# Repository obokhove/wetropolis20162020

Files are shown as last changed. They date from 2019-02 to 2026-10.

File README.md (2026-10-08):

# Wetropolis Design 2016-present & Wetropolis spin-off projects (scroll down)

## Introduction
The Wetropolis flood demonstrator is a conceptual, physical installation showcasing what an extreme rainfall event is and how such an event can lead to extreme flooding of a city. A layman's introduction to Wetropolis is found in the following blog:
https://research.reading.ac.uk/dare/2017/07/25/wetropolis-flood-demonstrator/
Please read the blog first. Wetropolis is best experienced in person but, second best, please watch the following movies (from 30-08-2016):
- Exploring Wetropolis (movie for everyone October 2022): https://www.youtube.com/watch?v=rNgEqWdafKk
- News item October 11, 2022: https://mpecdt.ac.uk/exploring-wetropolis-an-extreme-rainfall-and-flood-demonstrator/
- a test to give a first impression https://youtu.be/1FIHFOn6IPQ
- the equivalent of the River Aire Boxing Day flood of 2015 with city flooding resulting from two wd's (one Wetropolis day wd=10s) of consecutive extreme 90% rainfall (so 18s of rainfall in 20s) https://youtu.be/N4Sp5gHXcz4
- EGU highligh article, peer-reviewed in international scientific journal (under education & communication): https://www.hydrol-earth-syst-sci.net/24/2483/2020/ (also read the interesting discussions under "Peer review")
- Impact Case Study Research Excellence Framework UK: "Flood mitigation: from outreach demonstrator to a graphical cost-effectiveness diagnostic for policy makers" 2021/2022. https://results2021.ref.ac.uk/impact/0ad7c1be-8e91-4aac-ab57-6c1e873cd3f1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" 
- Feedback from showcasings is found in the feedback folder: https://github.com/obokhove/wetropolis20162020/tree/master/feedback
- People travel around and showcase Wetropolis upon request and, these days, with adequate social distancing. Just contact us: onnobokhove@gmail.com (UK) & zweers@dds.nl (NL)

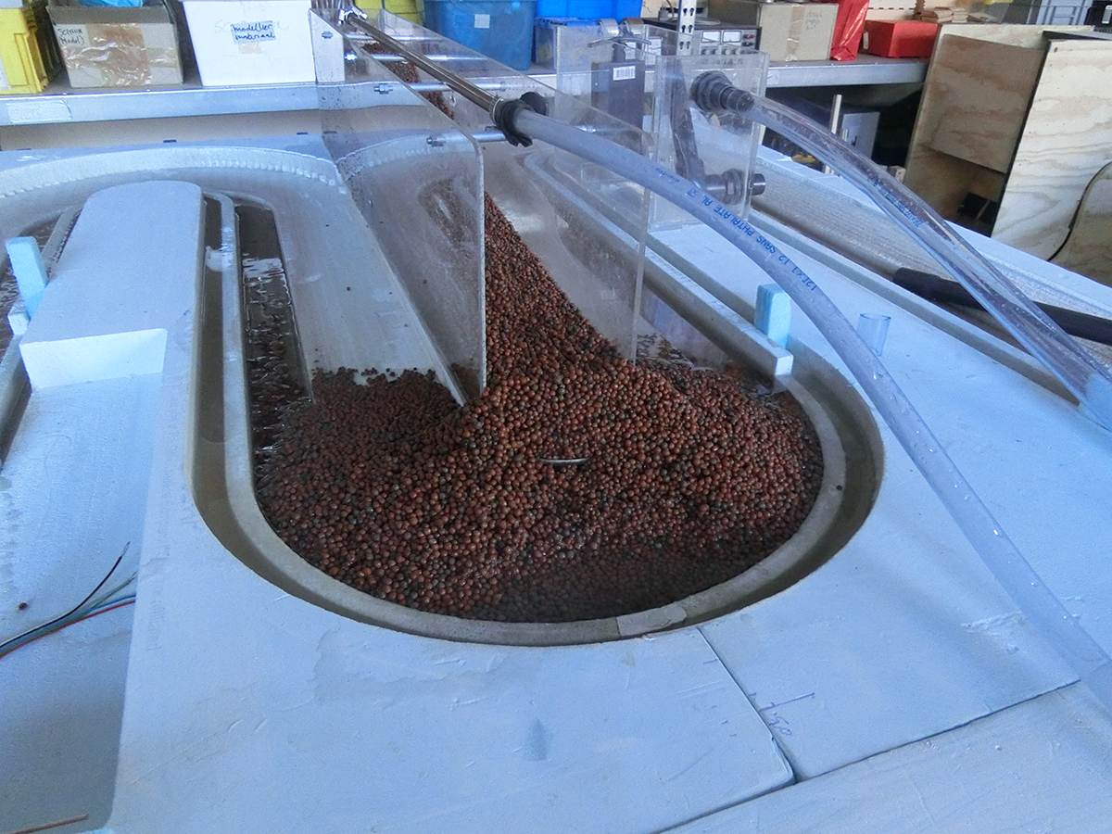
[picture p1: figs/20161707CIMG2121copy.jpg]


Wetropolis-I consists of several elements which we describe next:
- The topographic landscape with a winding river channel, one-sided flood plain, canals and the city-plain has been routed out of two standard polystyrene foam plates each of dimension 5x60x120xcm<sup>3</sup> (plus a small extra foam plate) with an overlay to fit two plates together. A smaller third piece was added to extend the river length after the city which enhanced flooding in the city plain. Drawings have been made in the CAD programs Rhino/Grasshopper and used to steer the router. Routing precision is circa 0.8mm. After the routing, the river channel and its flood plain have been roughened by gluing fine sand to the base, after which it has been varnished with yacht varnish. Specs: https://www.gamma.nl/assortiment/isolatieplaat-polystyreen-xps-120x60x5-cm-4-stuks/p/B133540 Isolatieplaat polystyreen XPS 120x60x5cm<sup>3</sup>
- A framework of wooden support slabs has been made that fits on four A-frames. This framework is put together with a bolt-nut system such that it can be disassembled for transport. Wooden wedges are used to squeeze and level the foam pieces within the slab-framework. The three foam pieces are squeezed together to limit leakage.  Aluminum one-side-sticky tape is used locally to seal two sections of the river channel together and thus bridge two adjacent channels. Rather than sealing off all leakage, which in practice becomes impossible, an "aquifer" system of two interconected gutters underneath the seams of the foam pieces leads leaked water back to the holding resevoir with the three aquarium pumps. Hence, the water budget is closed in the absence of evaporation, the latter which is negligible on the time scale of operation, of typically one to a few hours.
- Three aquarium pumps with a maximum pumping capacity of 0.375ml/s are placed in a holding reservoir, a rectangular bucket with dimensions ~0.3x0.40x0.22m<sup>3</sup>, which bucket is hung under the wooden framework in a rectangular area adjacent to the upstream inflow point of river water. Plastic tubing with inner and outer diameters of circa (1.8,2.2)mm leads the water from this reservoir to the upstream point and, depending on wether it rains or not, to the reservoir and the moor. Rainfall in the moor is spread out and visualised using a copper pipe with numerous downward-facing holes over the lava grit. Specs: Syncra 1.5, 234-240V, 50z, 23W, Q-max=1350l/hr, H-max=1.8m.
- The moor unit is made of acrylic and on the open side-face of the box a gauze prevents the lava grit from avalanching into the river. The acrylic reservoir is open from the top and water can enter through a hole near the top edge. Outflow of water in the river is regulated via an internal pipe which outflow level can be manually adjusted. Hence, active flood control can be demonstrated by manually adjusting this outflow level. Via an adjustable valve, outflow into the canal can be arranged separately. Note that this is slightly different from the set-up in the mathematical and numerical design model, where the outflow of moor water was partitioned between the river and canal.
- The set-up for the Galton boards including the Galton boards themselves, the accompanying Arduino control units, power sockets and plugs to operate the three aquarium pumps. The two draws from the discrete probability distribution are either computer generated or determined from the random paths of (a) steel ball(s) through the two asymmetric Galton boards. In the latter case, the steel ball triggers a signal by interupting optical sensors in one of the four channels on each Galton board. The signal subsequently steers either the reservoir pump, moor pump, both or none as arranged via the Arduino technology.
  
What follows next are:
- links to other sites with some material, partly duplicated here,
- links to the matlab design codes,
- technical specs of programs used in the routing and the router,
- information and files on the arduino design,
- funding acknowledgments and references, and
- the more-or-less chronological story of the creation of Wetropolis; it contains the basic information, often *in Dutch* (i.e. in italics), with accompanying translation/adaption in English, of various steps and issues we faced in the design. This information may later be ordered differently. Suggestions and questions are welcomed.

## Location of design files for the Wetropolis Flood demonstrator
The original design files for the Galton boards are found at https://grabcad.com/mylibrarymodels search for Wout Zweers and then Galton board 2016. Note that there are 2018 updates used for a new Wetropolis design. For the landscape CAD designs see https://github.com/zweers but some files have been or will be redeposited here as well in the folder topodrawings e.g. image (```sketchbase```) with on the left measurement points indicated which are given in the excel file. 
sketchbase

## Matlab file of mathematical and numerical design model 
The first code was created between 28-05-2016 and 01-06-2016 for OBs seminar at Imperial College on 01-06-2016. This first version was completed on 08-06-2016; continued further till 19-02-2018. The old version from 05-06-2016 is ```Codes/tabletopt1v2016.m``` (probably with the infamous error) and newer/newest version is ```Codes/tabletopt2v2016.m```. Version-3 from March 2019 contains simple label changes from curvilinear along-river coordinate x to s, see ```Codes/tabletopt3v2019.m```, to streamline notation in the article.

## Topographic landscape polystyrene plates, CAD files (2016)
The CAD programs used are the following: Solidworks for designs, saved as Step file for import in Rhino (V5); plugin in Rhino for routing: Rhinocam 5, which generates routing/freesfiles (NC files); routing is done on a BZT 1400 PF router/frees with Winpc-nc driver.
Browse the date-marked files in ```/figs``` folder for a photographic tour of the design. See the readme in the topodrawings directory.

## Arduino board and codes for automated internal Galton boards (2016-2018)
See file: arduinofil/schakelaar_kogeltjes_galtonboard-V0.12-30_aug_2016.ino (30-08-2016) and arduinofil/galton_board_november_2016-V02.1.ino (November 2016).
The print designs for the Arduino boards are found as pdf and dxf files dated 12-11-2016 (layoutprintplaatgaltonboard12nov2016.pdf and layoutprintGB12nov2016zwarteprintlijnen.dxf) See the readme in the Arduino2018 directory and the arduinofil directory for more details.

## Funding
The first version of Wetropolis was an outreach project within the EPSRC Network Maths Foresees EP/M008525/1 (2015-2016); the outreach project funded Tom Kent and Wout Zweers, circa 10k plus travel and transport and 2.5k for an update of the Galton boards (2017/2018).
A summary report from May 2018 is found under outreach projects here: http://www1.maths.leeds.ac.uk/mathsforesees/projects.html and here: http://www1.maths.leeds.ac.uk/mathsforesees/outreachprojreportwetropolis20162017.pdf
<!-- The writing of the journal paper and the creation of this github in 2019 falls under the EU project "Wetropolis: tangible education and watermanagement", see https://www.wetropolis.nl
The Natural Flood Management Wetropolis flood demonstrator, in short Wetropolis NFM, is to date (March 2019) under construction, and received funding from the CDT in Fluid Dynamics (Leeds), JBA Trust, the School of Mathematics and the School of Civil Engineering from the University of Leeds. Wetropolis NFM contains different elements: foam plates, FisherTechnique marble run and Arduino by Wowlab (Ir. Wout Zweers), Hydrotec Consultants Ltd (Leeds-Bradford), with assistance and direction by OB. More on Wetropolis NFM below.

Work Jan-June 2019:
- establishing this GitHub-site such that the Wetropolis flood demonstrator design is a) reported & b) can be used by others for modification & inspiration with Wout Zweers (Jan-March 2019);
- write-up & submission of scientific article on Wetropolis (outreach & education), presently submitted to HESS; see link below under references (Jan-March 2019)
- creation of poster for presentation at EGU2019 in Vienna with Bokhove, Kent, Zweers and De Poot (March-April 2019); and,

(ii) Work Aug-Oct 2019:
- further work on Wetropolis NFM modification & improving the Galton boards with Wout Zweers (continued till Sept 2019);
- work with Wainfleet Flood Action Group, invitation & report --see report below with input from Wout Zweers (Aug 2019); -->

Future possible plans:
- Making a groundwater Wetropolis with Galton boards & (two) conceptual groundwater cells, concerning groundwater flow below Enschede;
- promoting & refining the Galton boards further; and,
- further mathematical & numerical modelling;
- work with Wainfleet Flood Action Group, invitation & report --see report below with input from Wout Zweers (Aug 2019).

## References
- https://westleedsdispatch.com/government-flood-defence-proposals-kick-in-teeth-for-kirkstall/ Plus comments.
- O. Bokhove, T. Hicks, W. Zweers and T. Kent (2020) Wetropolis extreme rainfall and flood demonstrator: from mathematical design to outreach and research. *Hydrology and Earth System Sciences*. https://www.hydrol-earth-syst-sci.net/24/2483/2020/ (```wetroarticle```) wetroarticle See also 2019 preprint: https://eartharxiv.org/59ymk/
Revised version found above as: (```wetroarticlerevised```) wetroarticlerevised and (```wetroarticlerevisedno2```) wetroarticlerevisedno2
- O. Bokhove (2018) Wetropolis flood demonstrator. Final report EPSRC Maths Foresees network outreach project: http://www1.maths.leeds.ac.uk/mathsforesees/outreachprojreportwetropolis20162017.pdf
- O. Bokhove (2017) Wetropolis flood demonstrator. Blog in Data Assimilation of the Resilient city -DARE- project: 
https://research.reading.ac.uk/dare/2017/07/25/wetropolis-flood-demonstrator/
- O. Bokhove, T. Kent, M. Kelmanson, G. Piton, J.-M. Tacnet 2019: Communicating (nature-based) flood-mitigation
schemes using flood-excess volume. River Research and Applications 35, 1402-1414 (open access). Preprint: (```preprintRRA```) preprintRRA (Upon request: link to GitHub site with various river applications, R, Matlab and Python template files and applications. Please email Onno Bokhove.)
-  O. Bokhove, T. Kent, M. Kelmanson, G. Piton, J.-M. Tacnet 2020: A cost-effectiveness protocol for flood-mitigation plans based on Leeds’ Boxing Day 2015 floods Water 12(3), 652. https://www.mdpi.com/2073-4441/12/3/652 and https://doi.org/10.3390/w12030652
- The 2020 article above in the Journal Water (and its 2018 preprint in EarthArxiv) stimulated the writing of a flood-evacuation plan for Xfit the Forge or rather, vice versa, (some information of) that flood-evacuation plan information made it into that article. The plan was used again on 09-02-2020 during Storm Ciara, see https://bardvantwenthe.wordpress.com/2020/02/13/kirkstall-flood-evacuation-during-storm-ciara/ and also a few days later, both by Xfit The Forge in Leeds and some surrounding businesses in the Kirkstall estate. The (at that point virtual) flood-evacuation plan was put into action on 26-12-2015, when we saved more than 5000 pounds (later in 2020 corrected to be at least 20000 pounds) of gym equipment, and was formally written down a few days later, based on that evacuation experience, JWs photograph and my timings on Boxing Day. An example how something practical stimulates research and vice versa research confirms something practical. That ~29-12-2015 flood-evacuation plan has been added to the file list here as BokhoveXfitplan.pdf
- Hydraulic modelling and data assimilation for Wetropolis (1st link July 2020) https://github.com/tkent198/hydraulic_wetro
- Bokhove, O., Kelmanson, M., Kent, T. 2020: A new tool for communicating cost-effectiveness of flood-mitigation schemes. Sept 2020 evidence for the UK Government, parliamentary Environment, Food and Rural Affairs Committee inquiry into flooding; inquiry link: https://committees.parliament.uk/work/107/flooding evidence link: https://committees.parliament.uk/writtenevidence/9641/pdf/
After two years, so two years after our 2018 archived report analysing LCC's 2017 flood-mitigation plans, we fianlly received in September 2020 some critique of LCC on the content of our work; our response is found here, basically a beautiful rehasing of the 2018 material and refuting all critique (we did to date 23-12 not get a response on our rebuttal, of course) (https://eartharxiv.org/repository/view/1283/) and the above 2019/2020 articles (with authors BKMPT) of the 2018 report: see (```UKGovLCCcombo```) UKGovLCCcombo
- Bokhove O. 2021: On Communicating Cost-Effectiveness of Flood-Mitigation Schemes. Proc. 31st European Safety and Reliability Conference, Sept 2021, Angers, France. https://www.rpsonline.com.sg/proceedings/9789811820168/pdf/134.pdf "...  The tool is designed to help both the public and policymakers grasp the headline options and trade-offs inherent in flood-mitigation schemes. It has already led to better understanding and decision making regarding flood defences in the UK, Slovenia and France, particularly where a number of alternatives are being considered. Three realistic cases -from the UK, Slovenia and France- will be reviewed, including insights on dealing with uncertainty and on the communication of multiple benefits of Nature-Based Solutions, followed by a Socratic-method dialogue." (... the latter dialogue was set up for our secret admirers.)
- *GitHub site with Excel/Python/Matlab and R codes for river flood data analysis, e.g. in above analyses (all freeware):* https://github.com/Flood-Excess-Volume
- Evidence in: https://www.newscientist.com/letter/mg24132131-000-youd-need-wall-to-wall-beavers-to-dam-floods/ Letter by J. Rand on 16-01-2019 in New Scientist. 
Podcast (mathematical argument raised in interview by OB at 3:30min ff.; MP3 file 5D3C020E_2_dwdownload.mp3 saved): https://www.dw.com/en/living-planet-beavers-triumphant-return-to-yorkshire/av-54025402

## Selected presentations
- O. Bokhove (2016) "Managing Risk in an Age of Extremes". Hebden Bridge "Science of Floods" event 2016; https://www.pennineprospects.co.uk/news/the-science-of-floods. See (```hebdenbridge```) hebdenbridge.
- O. Bokhove (2016) "Wetropolis flood demonstrator: on extreme rainfall & river flooding". Seminar in Oxford December 2016. See (```Oxford```) Oxford.
- O. Bokhove (2018) "Wetropolis' Flood Demonstrator: mathematical design & drowning by numbers". See (```EGUWetropolis```) EGUwetropolis. *Geophysical Research Abstracts* 20, EGU 2018-1974, 2018. EGU General Assembly Vienna.
- Onno Bokhove, Tom Kent, Henk de Poot, Wout Zweers 2019. Wetropolis: models for education and water-management of floods and droughts. Poster EGU Vienna April 7-11 2019. (```posteregu2019```) posteregu2019
- M. Kelmanson, O. Bokhove, T. Kent, G. Piton, J.-M. Tacnet 2019: Using flood-excess volume to assess and communicate flood-mitigation schemes. Presentation of water-management flood-mitigation cost-effectiveness analysis triggered by Wetropolis. (```presegu2019```) presegu2019 Pending more minor adjustments. 
- Bokhove, O., Kelmanson, M.A., Kent, T., Piton, G., Tacnet, J.-M. 2019b: Public empowerment in flood mitigation. Flood and Coast 2019, Telford UK, June 18th. Conference. Accessible presentation matching the above River Research and Applications article: http://www1.maths.leeds.ac.uk/~obokhove/coastriverfev2019.pdf and https://www.floodandcoast.com/assets/SpeakerPresentations/5-Bokhove.pdf
- See the feedback folder for comments by organisers of three events at which Wetropolis was showcased.
- Onno Bokhove (17-02-2020) Managing river floods in an age of extremes: should we be more worried? Imperial College Public lecture. Audio recording link pending. As part of: http://www.imperial.ac.uk/news/195539/planet-earth-alive-using-mathematics-understand/

## Wetropolis spin-off projects, including Wainfleet
- Cost-effectiveness analysis of flood-mitigation plans: see the work of Bokhove, Kelmanson, Kent, Piton and Tacnet in References and Selected presentations above.
- Advisory work for Wainfleet Flood Action Group (W-FLAG) based on 19-08-2019 visit to Wainfleet in Lincolnshire: (```wfag2019```) wfag2019 Will be updated/under construction.
- Representation, i.e. comments, on flood-easing proposal for Apperley Bridge (item SFFF 20-04-2021): https://publicaccess.leeds.gov.uk/online-applications/applicationDetails.do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

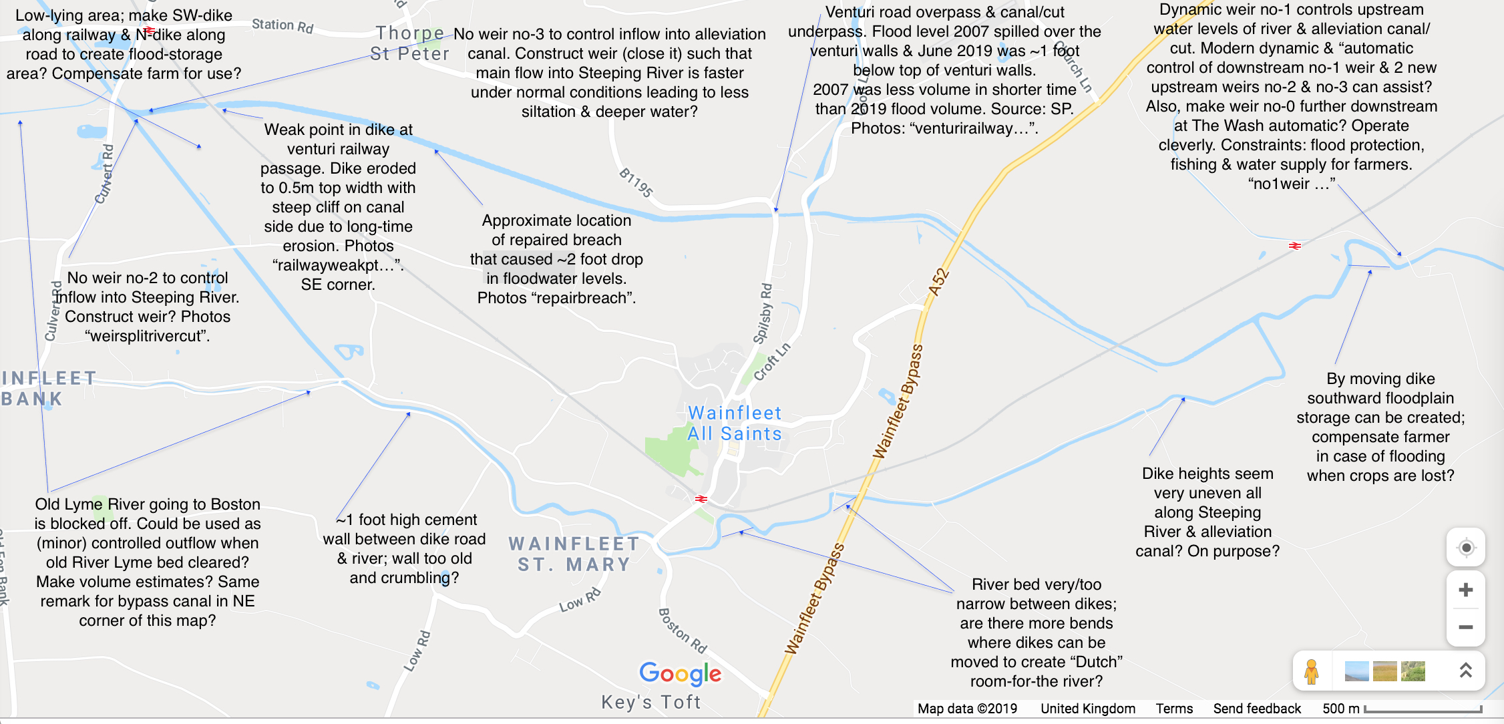
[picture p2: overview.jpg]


*Figure.* Overview map of the area, River Steeping and alleviation/relief canal around Wainfleet All Saints. North is upward. A distance scale is found bottom-right. We may be able to illustrate effect of dynamic weirs and "natural dredging" in a model set-up, invented by Wout Zweers and Jan-Jaap, and further enhanced by me.

----

# The story of Wetropolis' flood demonstrator

**_Mathematical/numerical design_**. While compilating the design files, we searched through our emails. A chronological account shows how the Wetropolis idea gradually grew to a definite design in a series of communications with Wout Zweers and visits to Wowlab as well as to two or three presentations:
- The presentation "Managing Risk in an Age of Extremes" at the Science of Flood workshop on May 8th 2016 in Hebden Bridge --see the file hebdenbrigde2016 -copy.pdf Please notice the first design sketch (```1stsket```) on page 18 and that the final design became quite different.
1stsket
- The presentation "On the Science of Floods: Rainfall, Flooding, and Flood Control revisited in the Design of a Table-Top Model" with the abstract developed in an email exchange with Dr Colin Cotter in which I promised a presentation and send him an abstract on 08-05-2015, before I had done any mathematical calculations. Talking about managing risk in the age of extremes!
- Note that the (in part raw) source material given below contains invaluable information on the design, which may be streamlined further at a later stage, but with the risk of losing some information.

**_Presentation at Imperial College_** 
"Sun 5/8/2016, 9:09 PM
Hi Colin, Would the following work for the June 1st seminar for MPE? (The abstract is a) Bit "experimental/preliminary" but I think I have enough for a good overview and discussion. Besides it coincides with the writing of the outline. Let me know your comments before I send it in, please. -Onno

Title: On the Science of Floods: Rainfall, Flooding, and Flood Control revisited in the Design of a Table-Top Model
By Onno Bokhove
Abstract: In a recent public event in Hebden Bridge, a town in Yorkshire that has seen a lot of sustained and flash floods over the last decade, I addressed the following questions:
- Is it going to rain more in the future?
- Can we define extreme precipitation and flooding events?
- How (well) can we predict heavy precipitation and floods?
- How (well) can we mitigate and control flooding?
I will elucidate the answers to the above questions and use them in the design and modelling of an interactive, conceptual table-top demonstration and experiment on rainfall, flooding as well as flood mitigation and control. The design will serve two purposes: as public demonstration of the concepts of flooding and as a simplified test environment for mathematical models of flooding with rainfall, hydraulics, hydrology, data assimilation and flood control. For the test environment, I will identify the mathematical elements involved to model "random" rain supply, channel/river flow, the hydrology of "Hele-Shaw valleys" (illustrating the effects porous moors, fast run-off from tarmac, and the function of reservoirs), flow in bypass canals, and control features such as weirs and sluice gates as well as data assimilation using a few measurement points. Obviously, this is work in progress."

- **_Mathematical/numerical design_**. Email Wout on 30-05-2106: *Maak ook maar zo’n model voor Twente. Er viel hier net 20 mm in 15 minuten. Zelfs de straat stond blank, ondanks de hoge ligging en vlak voor de keukendeur was het 5 cm diep water. En er komen nog een paar buien aan, wow!*
Please also make such a mathematical and numerical model for (rivers in the county of) Twente. Rainfall here a few minutes ago accumulated to 20mm in 15min. The street was flooded, despite its higher situation and in front of the kicthen door the water was 5cm deep. More rain is expected. Wow!

- **_Predesign_**. Email Wout 31-05-2016: *ik heb al materiaal gekocht. slang, klep, dik schuim, iets om detector mee te maken.*  Some materials have bought, in advance of the visit: tubing, a valve, thick foam, something to construct a waterlevel detector. Email Wout 04-06-2016: *Plaatje freesmodel*. The first design was on one foam plated with a DDR-style city. We routed it but it was abandoned since the channel and residence time was too short. See file (```Figovers''') overstromingsmodel-rendering-03.JPG
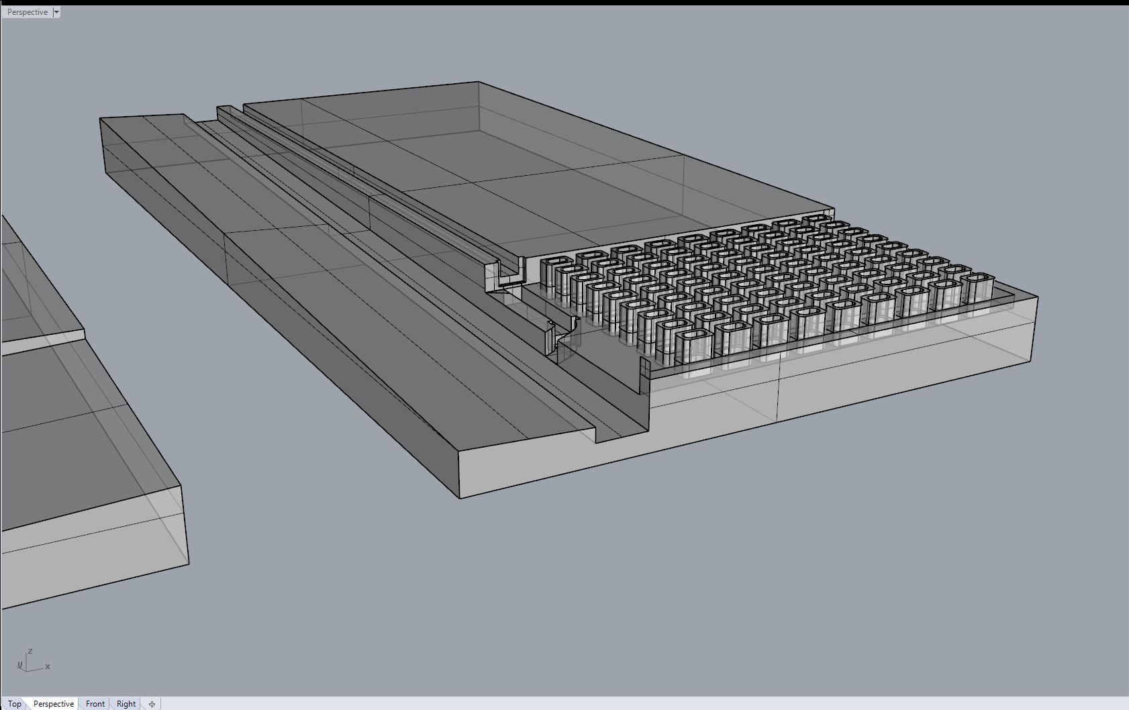
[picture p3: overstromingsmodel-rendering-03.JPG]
Figovers
 A simple water level indicator and pump controller using arduino and a relay: https://youtu.be/JJllc2UXyt8

- **_Mathematical/numerical design_** Seminar on Wetropolis design 01-06-2016: 'On the science of floods: rainfall, flooding and flood control revisited in the design of a table-top model' at Imperial College on 01-06-2016, where the first completed mathematical and numerical desig model was revealed -see the file reading1J2016.pdf At this seminar, I (OB) ran the matlab simulation at the end of the seminar for 100 Wetropolis days, i.e. 1000s real time, which is about 100s computational time. While there should be 2.73 extreme events on average over 100 wd's, in that simulation it was not till day 99 that the first extreme rainfall event and flooding happened. Meanwhile I was babbling for 99s waiting for the extreme event to appear, meanwhile sweating buckets while fearing that I had set up the simulation incorrectly. Then on day 99, the last day in the simulation, the extreme flooding event flooded the city. "Did you keep us in suspense on purpose, had you arranged this extreme event to occur on the last day", I recall Prof Darryl Holm asking. "Sure", I said, and smiled: "I did not. I was fearing that something had gone wrong but, hey, that is probability". I have saved a screen shot of this simulation with one spike on wd 99. See, indeed, the file (```simu''') simulator11ic.jpg
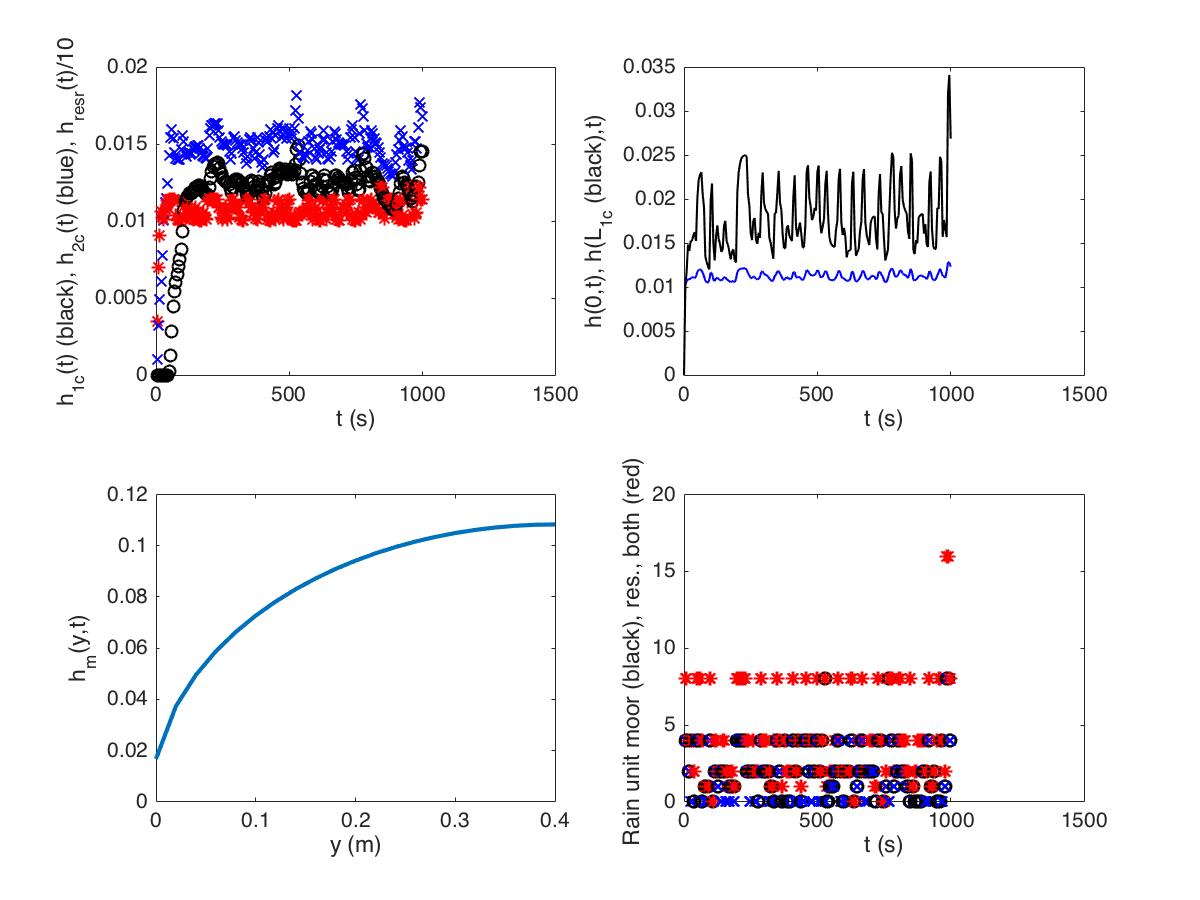
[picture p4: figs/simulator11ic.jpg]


- **_Galton boards_**. The test results of the first asymmetric Galton board (email Wout 30-06-2016): *Ik heb de aantallen even opgeteld. Na 10 x 16 kogels laten rollen:*

| | links | midden links | midden rechts | rechts |
|-----|---|---|---|---|
| trial uitkomsten | 28 | 79 | 44 | 9 |
| kansverdeling | 30 | 70 | 50 | 10 |

*Dus dat ligt aardig in de buurt* Fairly reasonable.

I have added the outcome of Galton board after 10x16 trials with the steel balls, I obtained the following after 16x1 trials with the steel balls rolling down a Galton board:

| | Left | middle left | middle right | right |
|-----|---|---|---|---|
|histogram of outcomes | 28 | 79 | 44 | 9  |
|actual distribution | 30 | 70 | 50 | 10  |

So the test and exact outcomes are fairly close. Test 15-07-2016: https://www.youtube.com/watch?v=FR3QPHajcew&feature=youtu.be
 
- **_Polystyrene topography_**. Four drawings/excel files of 2016 base plates (Email 07-07-2016 Wout) all dated with "20160707" in the file name

- **_Wooden suport frame_**. 21-07-2016 email Wout: the wooden support frame is getting ready; JPG-files started with 210702016 *Transportabel: alles kan goed uit elkaar, worden latten met wat uitstekende klampen in een richting, dus goed te bundelen. Grootste lengte: 180cm lat met 8 m6-boutjes om het vast te zetten de latten grijpen in elkaar en worden met een boutje geborgd (zie foto). Gewicht: het is hout*. The support frame is transportable. Reporting on dimensions and weight in order to assess whether the construction fits in the back of a car -with the backseat folded down. Longest wooden slabs are 180cm with 8 m6-bolt-nut pairs. The weight is substantial since the construction is made of wood.

- **_Testing the pumps_**. Test of river pump on 08-01-206: https://www.youtube.com/watch?v=GVCFESyP-mU&feature=youtu.be
*filmpje met eerste water in model. Rivier stroomt over bij debiet 1040 l  per uur en water in stad staat dan tot de rand waar de uiterwaard begint. Ik ga er een (instelbaar) 220 v pompje voor halen, ik heb nu 3 stuks  12V pompjes nodig (op 14V, dat houden ze niet lang vol) om dit debiet  te halen. rondpompen gaat verder goed. Ik heb een retourpomp op 220V welke het uitgestroomde water oppompt vanuit een teil/emmer op de bodem naar de  bak waar de 12V pompen in hangen (zo min mogelijk opvoerhoogte, maakt  het voor de pompen makkelijker om voldoende debiet te geven). Het pompje zal regelbaar zijn, zodat we de gewenste hoeveelheid ook vantevoren in kunnen stellen.* Movie with first flow in the model. Discharge is 1040l/h for which discharge the water is nearly flooding the city. Three pumps of 12V are needed but aquarium pumps working on 220V may be required. Top view of river-flood model in a test with the pump supplying the river water on 01-08-2016: https://youtu.be/QiVPV9ntBt0  The seams between two foam plates and the aluminum tape sealing them is seen nicely in here *overstromingsmodel test rivierpomp cyclus 1 augustus 2016*: https://youtu.be/Hwd3rjfHjkE

- **_Rainfall on moor_**. Rain tests 04-08-2016: https://youtu.be/cTSCZrBgIYs (and more rain https://youtu.be/cTSCZrBgIYs), and tests Galton boards (with a routing error in the bottom one Galton board, note that is symmetric instead of asymmetric -later replaced): https://youtu.be/zMG5POaJsHE

- **_Testing the pumps_** continued. And comparing my calculations of rain supply with what was measured: *Mijn calibratie kwam uit op 0.94l in 10 sec. Calculation spot-on dus. Op 4-8-2016 om 15:18 schreef Onno Bokhove: 1, 2, 4, of 8 R0/s over 10s unit. In mijn model had ik 0.12, 0.24, 0.48, 0.96 liter over 10s, en dus over twee cellen kan dat zelfs 2x0.96 liter zijn. Edoch mijn model is slechts indicatief." Wout: "de pomp werkte bij 8V en gaf 336l per uur. Bij 12V, net ook even getest,  kom ik op 550l per uur. Net voldoende denk ik, want bij 1000 liter per uur stroomde bedding net niet over bij de stad. dit getal klopt wel zo'n beetje met de eerdere tests van de dompelpompje: rond 500 liter per uur maximaal. De pomp stond op 8V, ik kan continu bedrijf (12V)  max een half uur gebruiken. Mocht het toch te weinig zijn dan stap ik ook hier over op een 220V pompje, voor ongeveer 25 euro heb je ruime keuze in debieten en geen gedoe met hoog amperage voeding voor 12V. het wordt toch via een relais aan uit geschakeld.* The actual calibration led to 0.94l in 10s, while the model predictions in 2016 were 0.12, 0.24, 0.48 and 0.96l over 10s, so for two cells that would be 2x0.96l/10s, even though these were indicative numerical estimates. The pump gave 336l/hr at 8V, 550l/hr at 12V, which seems just sufficient since the city was about to flood at 1000l/hr. Possibly 220V pumps are needed, which indeed were eventually bought, the aquarium pumps.

- **_Material for moor_**. Wout 11-08-2016: *Vandaag hydrokorrels gebruikt (grote maat, kon in de stad geen kleine  krijgen), valt niet tegen. Het gaat niet opdrijven, blijft goed in de  vorm. Het stroomt wat snel door en de vertragende werking en bergingscapaciteit komen niet zo duidelijk naar voren, maar nalopen  nadat de regen stopt is wel duidelijk te zien. Het vult tot ongeveer 7  cm hoogte met water bij ingestelde debiet, daarboven is het onverzadigd. Ik denk dat ik morgen wat fijner materiaal ga halen bij een tuinzaak, in  de stad hadden ze het niet. Wel heel fijn materiaal (leisplit en zand) maar dat stroomt niet snel genoeg door en dan krijg je vooral runoff. Daarmee kan ik dan wat beter kijken naar de respons op een regenbui, karakteristieke tijd, waterweerstand van het geheel maar zo, op gevoel, werkt het ook al aardig. De kraan voor het instellen van het rivierdebiet werkt goed, ruime  variatie mogelijk. Voor het reservoir heb ik nu een bakje met 2.5 liter gebruikt, dat was voorhanden, maar lijkt een bruikbare grootte te zijn. Bij leeggieten en moor aan krijg je geheid een overstroming, als je het leeggiet en de moor staat niet aan / druppelt niet na dan loopt de rivier vol en overstroomt wel in de iuterwaard maar Leeds blijft droog. Beetje mee spelen dus, wat gevoel voor krijgen. Moor aan en reservoir overdoen  geeft een flinke overstroming, maar pas nadat de berging van de rivier met uiterwaard zelf ook gevuld is. Voor het reservoir wil ik ook een plexiglas bak lijmen, en er een flinke schuifafsluiter op zetten. Alternatieve materialen zijn overigens: glasparels (straalkogels) van  1.5 a 2 mm, keramische ringetjes (filtermateriaal voor koivijvers), kunststof straal grit (ongeveer 1.5-2 mm diameter).*
Final set-up:
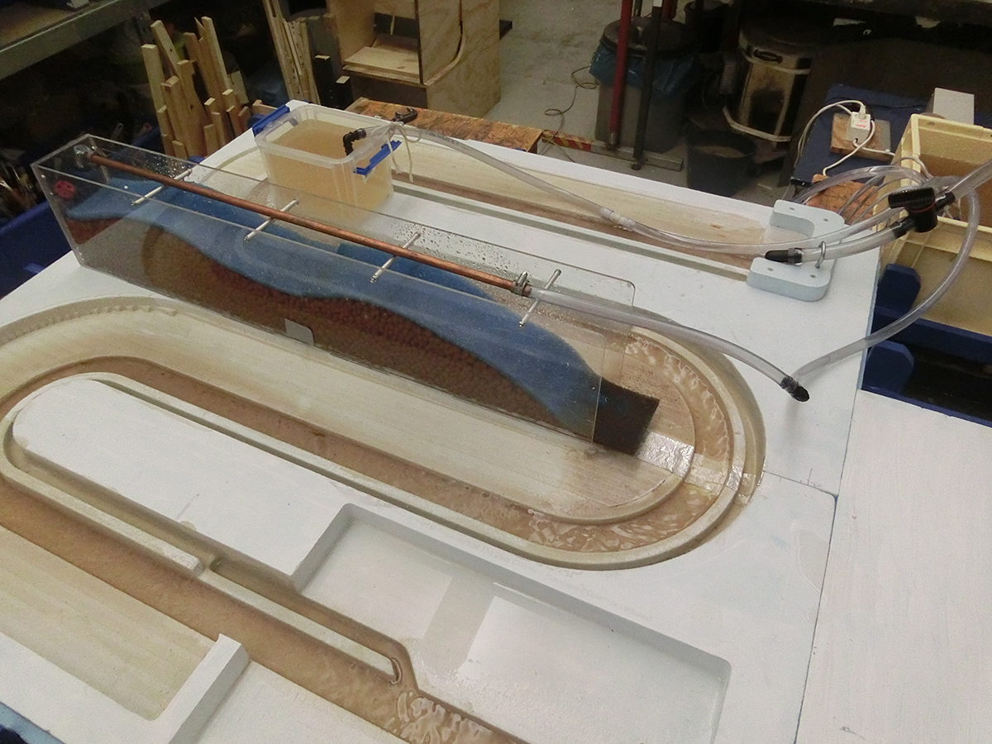
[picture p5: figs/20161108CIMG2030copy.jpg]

Hydrograins of bigger size were used in the moor. They don't float. The through-flow seems perhaps too fast. The moor fills under 8s rainfall to a groundwater level of about 7cm, above which the ground is unsaturated. Much finer material such as loam and sand is too compact and leads mostly to run-off. Intermediate coarse material will be considered next. (In the end we chose lava-grains, for which the e-folding time is about 20s to 30s, so a few wd's). For the reservoir a 2.5l unit was used, with a valve regulating the flow into the river. Eventually a new plexiglass unit was made with two exits, one adjustable pipe for the river and one valve for flow into the canal. We can still explore the use of alternative materials for the moor: glass pearls, ceamic rings (for koi ponds), and plastic grit.

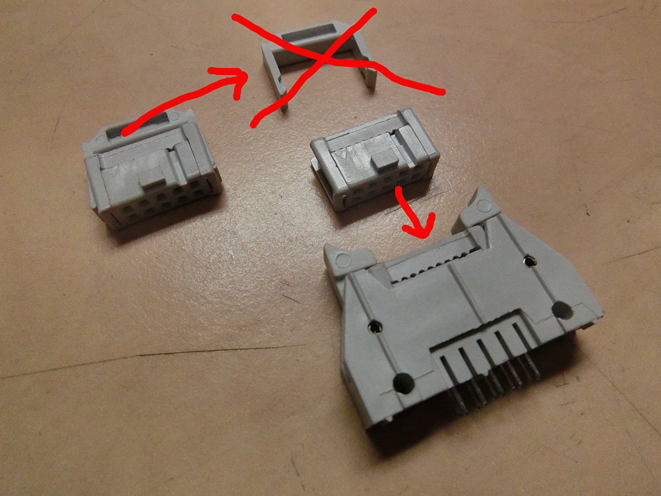
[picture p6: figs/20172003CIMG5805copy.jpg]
fotoboard2017
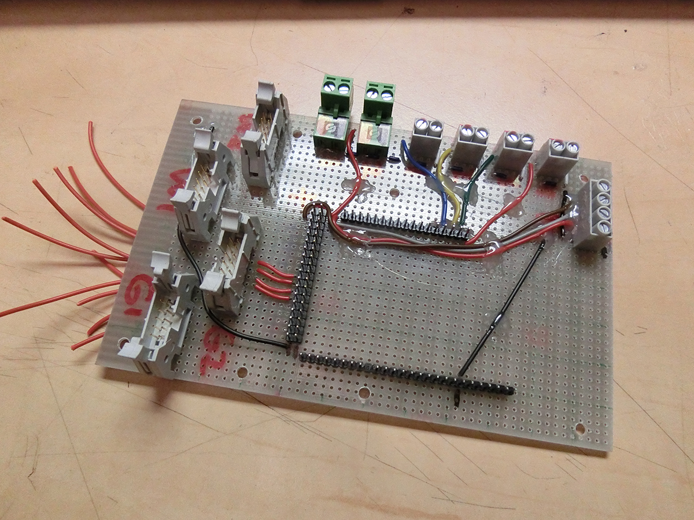
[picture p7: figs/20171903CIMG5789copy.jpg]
fotoboard2018
- **_Arduino boards_** The Arduino mother board was broken and patchy so a repair was underway. Wout 20-03-2017: *Er is een verandering: de stekkers aan de lintkabel zullen iets veranderd moeten worden. Het extra beugeltje wat de lintkabel terugbuigt moet bij drie van de vier stekkers worden verwijderd om te passen. Dat kan met een schroevendraaier of mesje, je kunt ze er zo afwippen. Ik had geen hoge maar lage chassisdelen meegenomen, niet aan gedacht. Zie foto* (```fotoboard2017```): *beugeltje (U-vormig) verwijderen, dan past de stekker onder de grendels. De aansluiting voor de relais (witte blokje met 4 aansluitpolen) is verplaatst op het bord, dat kwam beter uit.* There is a change for the plugs on the stripcables. The extra clips on three of the four stripcables need to be removed in order to fit. That can be done with a screwdriver or knife, to remove them. See the photo: remove the U-formed clip, then the plugs will fit under the locks.  and also  *Losmaken en verwisselen Arduino: Stroom er af! Neem de Arduino voorzichting van het oude moederbord, ik gebruik vaak daarvoor een kleine schroevendraaier welke ik in een kier tussen arduino en moederbord pinnen zet, draai de schroevendraaier voorzichtig wat het bord omhoog wrikt. Zorg dat het geleidelijk en recht omhoog komt door niet op 1 plek omhoog te wrikken, maar langs meerdere pinnen te gaan. Zo houd je de pinnen recht en heel. Plaats de Arduino boven de pinnen van het nieuwe bord. Controleer of alle pinnen recht zijn en goed tegenover de openingen van de arduino aansluitingen liggen. Het kan maar op een manier goed. Druk het voorzichting aan, niet in een keer de ene kant en dan de andere, maar afwisselend op verschillende plekken aandrukken zodat de Arduino gelijkmatig erop wordt gedrukt.* Removal and swapping of Arduino-boards: turn power off! Then carefully take the Arduino out of the old (partially broken) motherboard, perhaps by slipping a small screwdriver in te gap between Arduino and motherboard. Lift it off evenly such as not to bend the pins. Put the Arduino on the new motherboard taking care that all pins are and stay straight. There is only one correct way. Press gently alternatingly on different spots to get it on evenly, and/or readjust.

- **_Polystyrene topography, sand and varnish to roughen river base_** Instructions 20-02-2019: *leverancier: Welkoop schelpenzand, agri retailo Galvanistraat 100 Ede, verkoop via Welkoop. Schelpenzand bevat gecalcineerd zand en zeeschelpen (sand and shells) voor aanbrengen is het zand gezeefd met een huishoudzeef, maasopening ongeveer 0.9 mm (vierkante opening), draaddikte ongeveer 0.1 mm; zand is vastgelijmd in een vrij ruim opgezette laag matte PU lak. Aanbrengen: de kunst is een gelijkmatige laag te krijgen welke goed hecht. De lak werkt als lijm. Breng lak aan met een volle, platte penseel, werk met hanteerbare oppervlakken. Horizontaal en verticaal kunnen tegelijk worden gelakt. In de natte lak is een overmaat zand gestrooid, door het schuim te wentelsen en het zand heen en weer te laten schuiven is een gelijkmatige bedekking bereikt op horizontale en verticale vlakken. De overmaat zand van het schuim laten vallen door het schuim op de kop te zetten en hier lichtjes op te kloppen. Ga verder met het volgende deel. De vorm is in gedeeltes bezand omdat het niet in een keer dik genoeg in de lak kon worden gezet zonder dat de lak wegvloeide (druipers of juist te dunne laag op verticale vlakken). Je moet dus vlot doorwerken en in een sessie het werk afmaken. Na bezanden en afkloppen de laag vooral niet aanraken tot deze droog is anders veroorzaak je klontjes welke niet meer vlak te krijgen zijn. Enige handigheid en vaste hand met de kwast is wel zo praktisch, maar het valt wel mee om een goede vlakke laag te krijgen op deze manier. 2-3 cm rand welke je later wilt aftapen (voor waterdichte verbinding) bij de overgang van het kanaal van ene naar andere schuim niet bezanden, tape hecht slecht op het zand en er zal water onder door lopen.* Supplier of sand-shell mixtire is the Dutch store Welkoop. The sand mixture was sieved with a sieve with holes of 0.9mm and wire thickness of 0.1mm. The sieved sand was glued on the Wetropolis river bed with PU varnish. It was applied as follows: key is to bring the varnish on in a homogeneous layer. The varnish works as glue and is brought on by  flat brush. Both horizontal and vertical surfaces were varnished at the same time. There is an abundance of sieved sand spread on the wet varnish. By dealing with the foam and shift the sand back and forth, one obtains a uniform layer. The excess sand is removed by turning the polystyrene foam upside down and by then tapping lightly on the foam. Persue this procedure one area after another. Several thin layers have been applied otehrwise the varnish starts dripping or the layer is too thin on the vertical faces. Work quickly and don't touch the layers befor ethey are dry otherwise one gets floculation. Near the edges of the riverbed to another foam a strip of 2-3cm is needed such that the aluminium tape can be taped on, so donot vanish and apply sands in this strip.

# Wetropolis Natural Flood Management 2017-2019
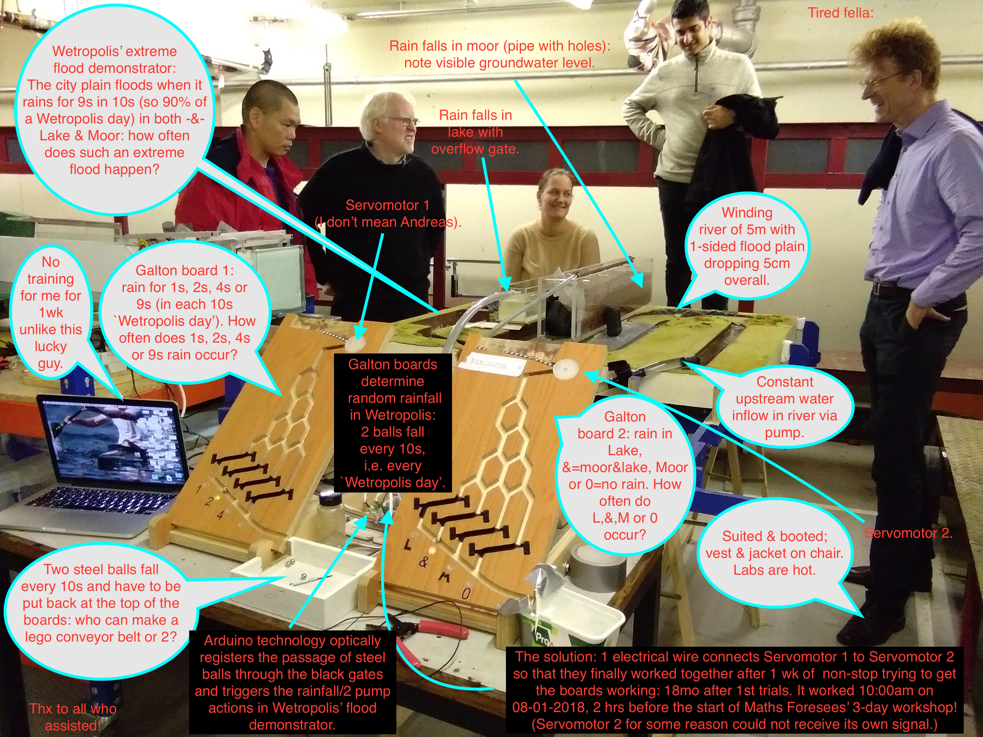
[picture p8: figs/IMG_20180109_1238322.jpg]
WetNFM
Of version 0 the base foam plates dissolved because water-soluable paint was used despite our warnings ... small showcasing at Maths Foresees network meeting January 2018. Cartoon of the entire Wetropolis set-up and its workings for an interim version of Wetropolis revisited with natural flood management. (```WetNFM```) 

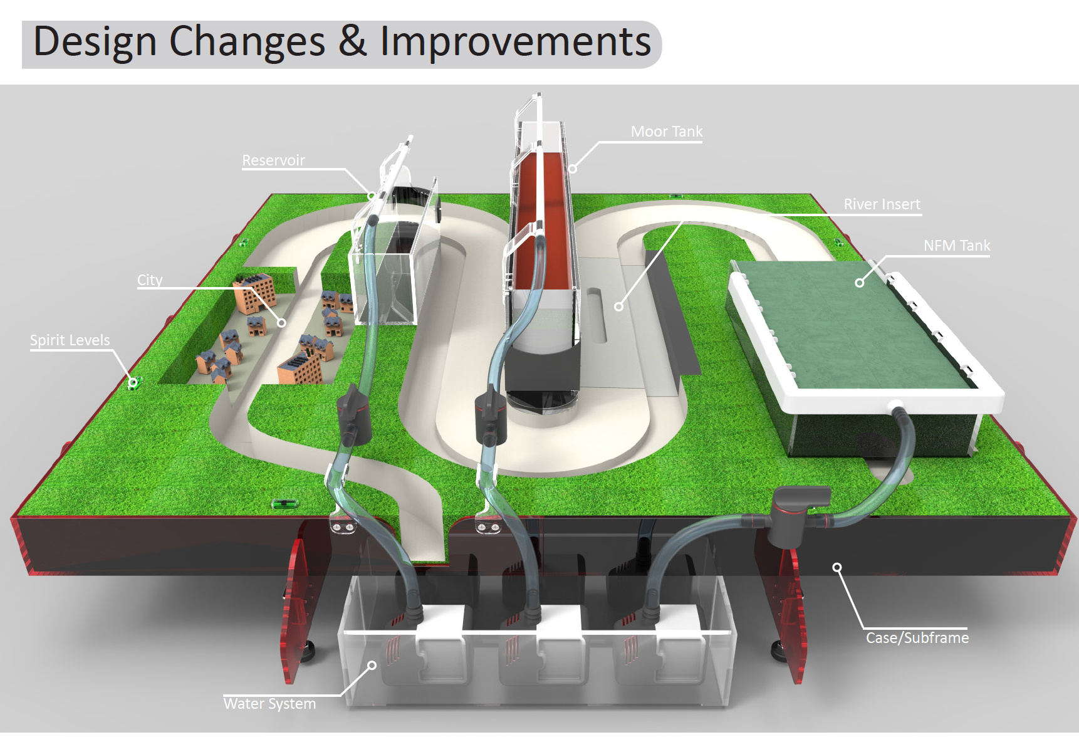
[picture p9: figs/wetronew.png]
A design sketch (```WetNFM2```) is given of the Wetropolis flood demonstrator revisited to demonstrate principles of NFM: it contains a river section in the middle of the set-up in which the effects of inserts of different roughnesses --smooth, medium and very rough e.g. concrete, gravel and trees-- can be observed as well as an upstream catchment with oasis that can be shaped to contain smaller channel fed with streams that can be blocked with leaky match-stick dams. The latter oasis landscape can be molded by the public and hands-on experience with leaky dams, their effects and their failure can be tested. Courtesy: Alex Hinxman. 

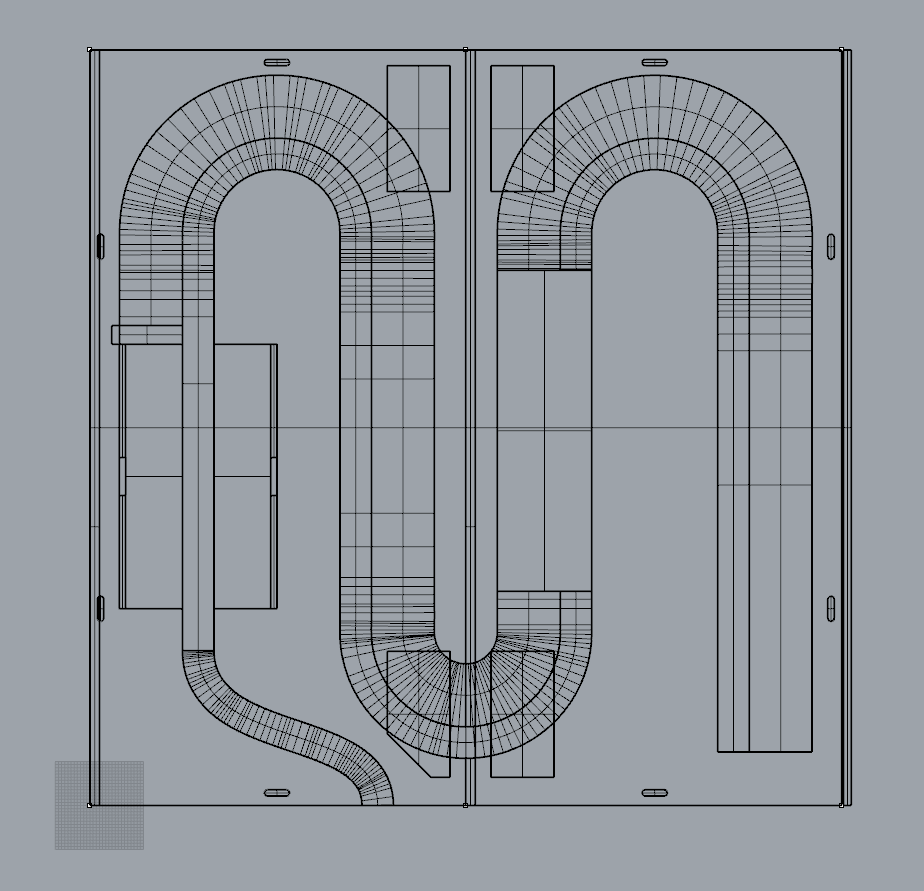
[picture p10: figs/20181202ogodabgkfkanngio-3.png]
newbase2018
A new topographic base-plate design is made (with some glitches) using new CAD software, see 02-12-2018 file (```newbase2018```) 
See also files starting 20180213 in folder topodrawings for several new design features: [topo2018](topodrawings/20180213overzicht1t10aanpassing.PNG)
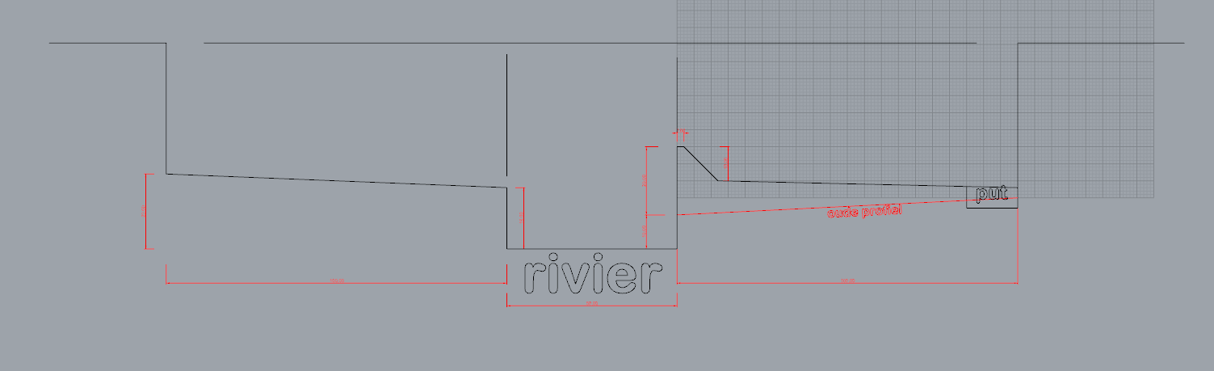
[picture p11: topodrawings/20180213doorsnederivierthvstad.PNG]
crosscity
New river and city plain cross section in (```crosscity```) on 13-02-2018: 

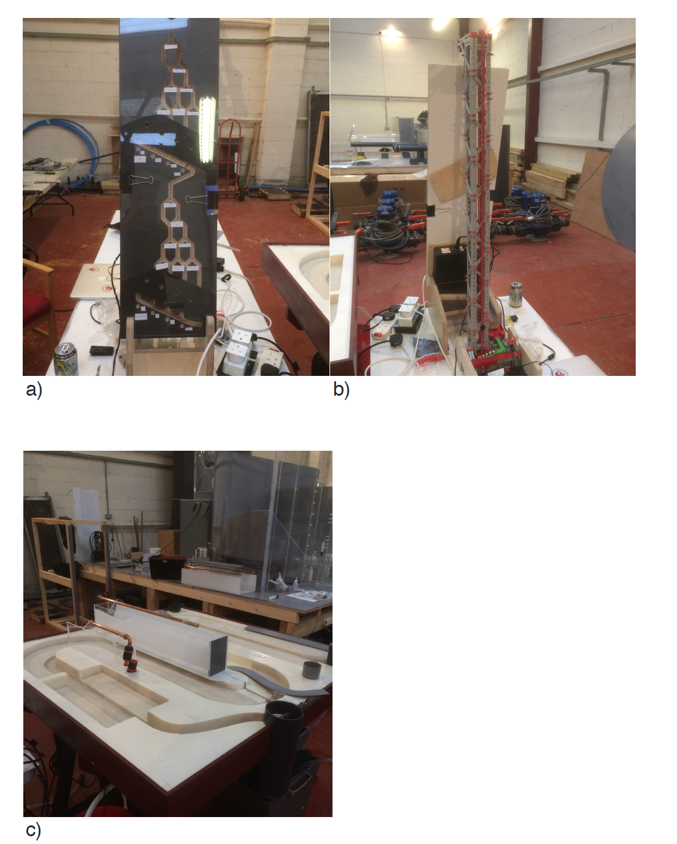
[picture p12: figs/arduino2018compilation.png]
NFMwet2
- **_Arduino board_** The folder ```arduinofile2018``` contains the Arduino codes for the 2018-design of the Arduino boards. New Galton board with four recirculating steel balls via a FisherTechqniue construction, a) front, b) back, and c) overview of new NFM topographic lanscape at Hydrotec Consulting (alas, the riverbed was not 1:100 but rather uneven so needs to be replaced) (```NFMwet2```): 

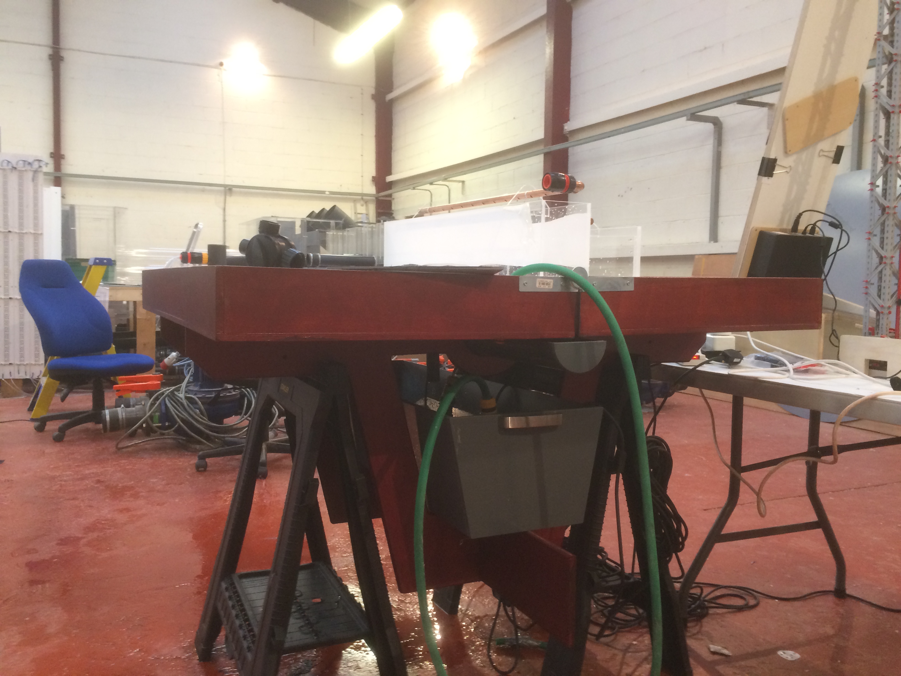
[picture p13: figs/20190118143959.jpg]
NFMwet3
Detail of the new reservoir, aquifer and recirculation units: (```NFMwet3```): 

<!--
## Assessment of flood-mitigation plans near Bradford and Leeds
- Early 2021 a representation was officially submitted to Leeds City Council (LCC) by me on the flood-easing plans for Apperley Bridge (part of Bradford City Council BMDC); see file PlansApperleyBridgefloodeasingUpdate.pdf; note that I am a Bradford citizen and our local Bradford  city counsellor suggested to me to submit my queries as official representation.
- After numerous emails to LCC, LCC commented by email that it did not need to respond to the queries raised in my representation because legally it is not obliged to reply to representations from organisations which are not part of a specified list. (Note that this response is in direct conflict with LCC's code of conduct which states that LCC needs to be open to scrutiny and accountability, unless LCC's interpretation of what accountability means is "interesting".)
- Hence, my queries in the representation about:
a) the flood-defence walls possibly being more expensive than earthen walls [indicated by cost tables of JBA & EA as well as advice by a Civil Engineer working on River IJssel works (The Netherlands) & a railroad engineer; also steel prices are high due to the war in Ukraine such that the use of local soil/clay is especially preferred, if it was not already the case],
b) the funnel being created in front of the Apperley Bridge by these new walls, under climate change, leads to an equal and higher chance of flooding of the houses on the South side of the river and the flood plain & road on the North side (arguably walls for the flood plain on the North side should be lower or absent); furthermore, the increased water pressure due to the water levels heightened by higher walls increases the danger that the bridge collapses under the pressure; and,
c) the Haigh Beck catchment sewage-laden water being trapped in the neighbourhood next to the river because valves would block the polluted beck water from entering the River Aire, during high river levels; all these points (a,b,c) were not responded to and possibly ignored.
- A recent written official data-request inquiry (October 2022) at BMDC revealed that BMDC had given all rights to build flood-defence works on Bradford council soil to LCC and that BMDC could not be held accountable in that BMDC had no longer any say in the matter. Is that legal? BMDC refuses to say who within BMDC gave the BMDC rights away to LCC (I made an official data request asking for a clarification). BMDC also indirectly admitted the oversight on (c) in that a consultant had been appointed by BMDC (info Oct 2022) to deal with the beck water flooding the Apperley Bridge neighbourhood next to the river, at high river levels (see also several posts of polluting events on my youtube & twitter channels: https://www.youtube.com/channel/UCgtjNTlzp0hZQznFAaF92WQ). Note that (one person of) Yorkshire Water (YW) has asked me to report pollution incidents of Haigh Beck.
- Recent inquiry with Yorkshire Water (October 2022) also revealed that LCC & BMDC had "forgotten" to include Haigh Beck floods from the flood-protection works in 2017-2021, except that I had warned them about the issues both in 2020 and officially in 2021.

- Note that the first October 2018 comment at the bottom of https://westleedsdispatch.com/government-flood-defence-proposals-kick-in-teeth-for-kirkstall/ led (one high-ranking person of) LCC and (one high-ranking person of) UoL to submit complaints against me and my team, which led to warnings, also in writing, by management (see also the Bokhove et al 2020 article in Water, which backs up that there are, verbally admitted, inconsistencies in LCC's flood-mitigation plans --needless to say we first asked LCC for comments and got none before any reports were made public (LCC and consultant expressede no interest); also the final articles in the journals Water and River Research were in the end commented on by LCC's consultant but next to nothing had to be added since the articles were correct). After the REF impact case was largely finished I suggested (Sept. 2020) to UoL management and HR two options: (i) to either punish me and my team for the "crimes" committed (according to the complaints by one person of LCC and one person of UoL --note that the complaints by LCC were backed up by a team of engineers, a board member within LCC and the local EA lead as well as a consultant) or (ii) to fully and in writing take away the warnings (which was done only and reluctantly without any apology to me and my team after I involved and was advised to involve the union). In addition, I had put in a countercomplaint rebutting the complaints by (one person of)LCC and (one person of) UoL, in Jan 2021, with the request to investigate the procedure to prevent putting pressure on researchers based on false complaints, especially stressing the importance that such pressure strangles the discussion on the -in-the-UK-much-needed- sustainable flood-protection works. To date (30-11-2022) UoL refuses to deal with this request, in fact, has verbally rejected the request and stiffles all discussion on the issue. Regarding all written and verbal informal (Sept 2020, January 2021, May 2021, November 2021, etc.) and formal complaints (July 2022) I have submitted, the UoL protocols thereon are factually ignored (to date 30-11-2022). Academic freedom and freedom of expression are seemingly meaningless concepts when high-ranking people decide otherwise? Note that the research found in our reports, articles and REF impact case reflect the efforts of an international team (from UK and France, Europe), with the REF case having a UKRI score of at least level 3 (out of 4), since our work is and has been used in practice. Of course, management invited me (by email) to put in a formal complaint if I did not agree with their mostly verbal statements/response. So I did, by invitation. To date, as far as I know, the formal complaint of July 2022 disappeared, with delay tactics being an effective mechanism. My first complaint has a simple resolution, and such a resolution suggestion is mandatory: to provide me with the notes of the verbal conversations that took place, which request according to written regulations is allowed, should be complied with; notes about informal verbal complaint discussion should be made and sent out as standard practice, certainly when requested.

Why would one be so foolish to analyse council flood-mitigation plans? I have become such a fool because I first hand experienced the devasting power of a a flood and the damage it causes. Otherwise said, I care while one should noot care, apparently. That is, I called the flood-evacuation of Leeds' Crossfit gym in Kirkstall on Boxing Day 2015. That day, eight people arrived late circa 15:00 on 27-12-2015 at the the Crossfit Leeds gym, since nobody in Leeds had a key and the owner Mike had to come from Redcar. The water had already entered the premises around 12:30. We worked non-stop for three hours to bring the gym equipment to dry levels upstairs or on the pull-up racks. At 18:00, I called an end to the evacuation, see the photo below, since the water-level was still rising. Mike took the group photo found below. Wading back through hip-deep fast-flowing waters of the torrent that once was Kirkstall Road left a deep impression on us. It made me wonder whether the flood damage could have been prevented and why the flood plains were build-up with businesses the way they are, without raising them on 1m to 1.2m mounds. Logically yet foolishly, I then looked into the flood-allevation plans from LCC from 2017 onwards. We saved 20000 pounds of gym equipment that Boxing Day and Mike kindly gave a statement how my call and impromptu flood-evacuation plan had mattered, see the REF impact-case study. The rest you know.

Would I do it again, given all the harassment I have faced and continue to face via work and councils? That is a good question. After all, it is more peaceful to do exactly nothing and be part of the silent majority. I apologise for making all these mistakes. I apologise for caring about the public.

## Ad hominem and responding to tone

Xmas party response of a colleague who I told the above: "Ad hominem".

See Graham's hierarchy of disagreement, also including "responding to tone", both used "rather than addressing the substance of the argument itself":
https://en.wikipedia.org/wiki/Paul_Graham_(programmer)#/media/File:Graham's_Hierarchy_of_Disagreement-en.svg
and
https://en.wikipedia.org/wiki/Paul_Graham_(programmer)#Graham's_Hierarchy_of_Disagreement

-->

The idea of Wetropolis arose after the 26-12-2015 Boxing Day flood evacuation of the Crossfit Leeds The Forge gym --photo below at 18:00 afer we saved over 20k GPB in gym equipment from damage-- in combination with a subsequent request by the (national) EA and JBA Trust later in 2016 to visualise what a flooding return period is:
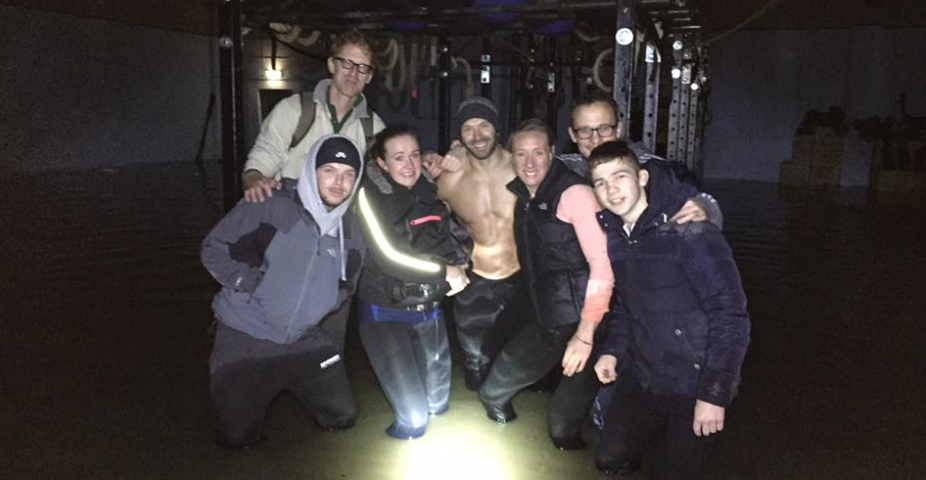
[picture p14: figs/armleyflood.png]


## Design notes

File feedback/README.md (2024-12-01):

# Wetropolis Showcasings and Feedback

Well over 1000 people have now experienced in person what a return period (or ``Annual'' Event Probability) is for an extreme flood by viewing the Wetropolis Flood Demonstrator in action.

## Wetropolis showcasings
- 5/7-09-2016, Edinburgh, General Assembly of Maths Foresees Living with Environmental Change (LWEC) Network. Presentation on Wetropolis and public engagement: http://www1.maths.leeds.ac.uk/mathsforesees/edin/MFEdinb2016s.pdf
- Two (September 2016 and 2017) induction days of the Leeds’ fluid Dynamics CDT (Onno Bokhove & Tom Kent; Robert Long, Craigh Duguid and Duncan Livesey); post 22-09-2016 at https://www.facebook.com/resurging.flows
- Two afternoons as part of the public exhibition on the Boxing Day 2015 floods in the Leeds’ Armley Musuem (Dec. 8th 2016 and March 26th 2017), with Tom Kent, Tiffany Hicks and Onno Bokhove and asistance of CDT Fluid Dynamics’ Leeds PhD students Thomas Goodfellow, Robert Long, Craigh Duguid and Duncan Livesey. Post 05-12-2016 at https://www.facebook.com/resurging.flows
- Presentation on Mathematics of extreme events and showing of Wetropolis the public flood conference by the Churchtown flood action group on 28-01-20217 with Valerie Zwart, Tom Kent and Onno Bokhove; in front of 140 flood victims and some experts on flooding https://www.facebook.com/Churchtown.flood.action.group/ & post 16-01-2017 at https://www.facebook.com/resurging.flows See announcement in: https://www.thewestmorlandgazette.co.uk/news/14975893.list-of-post-floods-work-to-becarried-out-in-cumbria-this-week/
- CDT students Robert Long, Craigh Duguid and Duncan Livesey, Liverpool at: The Merseyside Flood and Coastal Erosion Risk Management (FCERM) Partnership Workshop on: Collaborative Natural Flood Risk Targeting Maps. 08-03-2017.
- Be Curious Science festival Leeds 2017; with Wetropolis mentioned in the call.
- Second Study Group of our network Maths Foresees at Turing Gateway of Mathematics, Cambridge by Robert Long, Craigh Duguid and Duncan Livesey; post 07-04-2017 https://www.facebook.com/resurging.flows More below.
- Showcasing as iCASP confluence Leeds, June 2018.
- Wetropolis II at Mathematics of Planet Earth Exhibition 15-02 to 23-02 2020 www.imperial.ac.uk/news/195539/planet-earth-alive-using-mathematics-understand/ More below.
- Wetropolis II at Mathematics of Planet Earth Exhibition 28-05 to 05-06 2022. Coming up: https://mpecdt.ac.uk/mathematics-of-planet-earth-exhibition-2022-2/
- See also below.

## 1. Wetropolis I: Feedback (21-12-2019) from Churchtown Flood Action Group 
The Churchtown Flood Action Group won the Environment Agency Project Excellence Award in 2018 and is the foremost Flood Action Group in Lancashire.

"Dear Onno, 

Obviously I would like to help you in any way that I can. When you gave your talk at the original Conference [January 2017] that I organised, I thought, despite its complexity you made it understandable through the use of the Westropolis model. But I only have GCSE Maths, so I just couldn’t understand the more complex calculations. I think I got the gist of your talk about Risk. I did learn from your talk that modelling is not an exact Science, because there are so many variables, to take into account. It is obvious that any system that makes the calculation of the risk of flooding more accurate is to be desired, especially in the present climate, when the flood risk assessments are in the hands of the people who produce them for their own use. The people who critiqued your article obviously have a greater understanding of what you are doing than I do. I am presuming that the Scientific Journal will not accept your article without some adjustments? 
The feedback that I have had from lay people is that your talk was enjoyable and the Wetropolis demonstration was interesting and informative. 

Regards, Siriol"

(Vice Chairman of Churchtown Flood Action Group. Administrator of Lancashire Flood Action Groups.) 

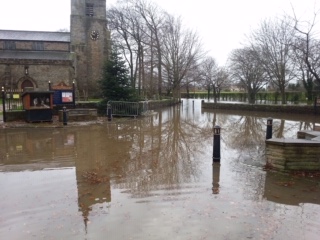
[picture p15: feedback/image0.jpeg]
PhotoCT
(```Photo via Siriol Hogg```) 

Video on Churchtown flooding: https://www.youtube.com/watch?v=il84G9XlS94

*Reaction*:
- Modelling is a(n exact) science. However, due to the chaotic nature of weather prediction and lack of uncertainty in the input parameters, as well as insufficient measurements and measurement erors, predictions have (a large) uncertainty, certainly long-term and climate predictions. Modelling is the science that includes dealing with such uncertainty.
- Indeed, publication in journals is an iterative process and in revisions one can address comments of the reviewers.

## 2. Wetropolis I: Feedback from Leeds Armley Museum 03-01-2020
“Wetropolis was utilised at a science event at Leeds Industrial Museum to complement an exhibition reflecting the community’s experience of the 2015 floods in the city. Being able to show the public how the flood occurred through the Wetropolis model certainly assisted the layperson’s  understanding of how the flooding occurred, making the mathematics of flooding accessible to a wider audience.”
Chris Sharp, Assistant Community Curator, Leeds Industrial Museum.

## 3. Wetropolis I: Feedback from Turing Gateway 28-12-2019
Wetropolis was displayed during the Environmental Modelling in Industry Study Group (April 2017 at the Isaac Newton Gateway to Mathematics in Cambridge) https://gateway.newton.ac.uk/event/tgmw41 with the following feedback “... the addition of the Wetropolis flood demonstrator on Wednesday attracted a lot of attention and interaction”. Jane Leeks from INI Gateway.

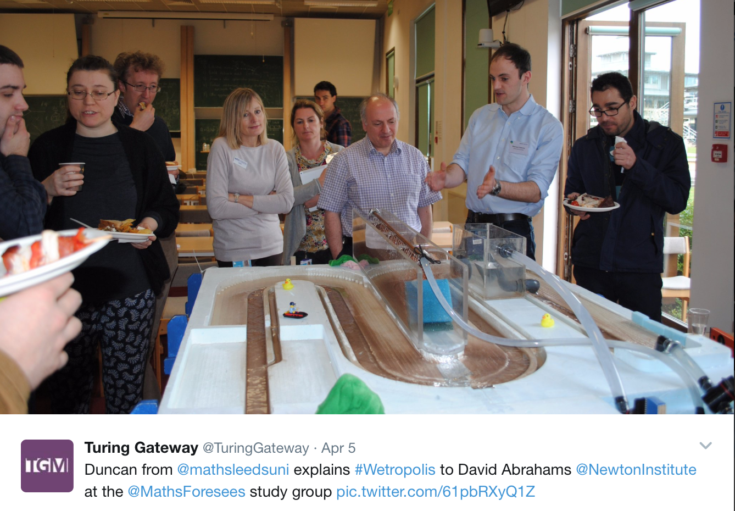
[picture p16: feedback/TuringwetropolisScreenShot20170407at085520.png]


(```Photo via Turing Gateway```) <!--![PhotoTG](TuringwetropolisScreenShot20170407at085520.png)-->

## 3b Wetropolis I: showcasing as iCASP confluence Leeds, June 2018

## 4. Wetropolis II: Feedback Mathematics of Planet Earth Exhibition 15-02 to 23-02 2020

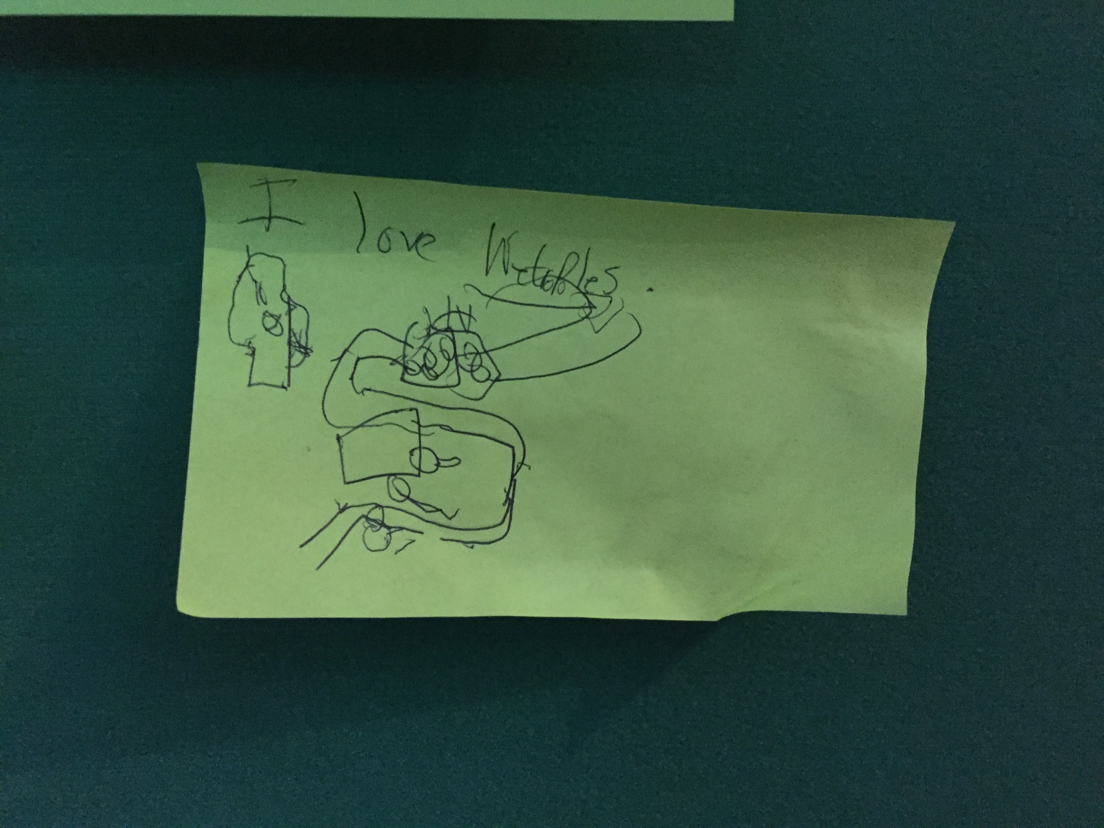
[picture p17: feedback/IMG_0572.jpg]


Learn more about "Planet Earth is alive: using mathematics to understand and protect our world", including "A day in the world of *Wetropolis*", written by Claudia Cannon: www.imperial.ac.uk/news/195539/planet-earth-alive-using-mathematics-understand/
There were on average more than 50 visitors per day, and often many more, so over 9 days circa 450 to 1000 visitors came to the exhibition.

Comments made on the feedback board; a big thank you to all feedback providers for the feedback below [*reply by OB=Onno Bokhove*]:
- Just awesome. Smart. Intuitive. Fun.
- I love Wetropolis. [*OB: See photo of drawing above by someone who played for an hour with Wetropolis and took 5 videos.*]
- I think this exhibit is great. Could you add a way to force a flood made with difffently weighted marbles/blocks in the marble path?! Would be funny to see -flood. [*OB: We are in the process of making a Galton board out of Lego, which would make different channel options easier to make/modify by the public. Different size/weight marbles would not make a difference since the pass-through is registered optically.*]
- This exhibit is very cool but could (you) also simulate tsunamis? 9 second moor/res for the win. [*OB reply: Our coastal wave-tank in Leeds can illustrate overtopping by coastal waves and inundation by tsunamis. Tank designed by team, including me, for JBA, see: https://www.youtube.com/watch?v=3yNoy4H2Z-o*]
- Brilliant visual & practical demo of flooding. Thank you.
- Really nice model of flood control, I like how everything is presented and I learned some new things too.
- Brilliant! So clear & captures the concept of chance in weather systems.Please construct more. [*Reply OB: the full and open design is found on this GitHub site and anyone is free to build a bespoke Wetropolis. Given lack of funding of outreach by UK funding agencies and universities, we are unable to build more ourselves.*]
- Wondering if bringing back the population of beavers is the most effective! Living in Dartmoor -the moor has it. [*OB reply: alas, no, their effect is much too small; see "Using flood-excess volume to show that upscaling beaver dams for protection against extreme floods proves unrealistic".* https://eartharxiv.org/w9evx/ Comment J. Rand in New Scientist https://www.newscientist.com/letter/mg24132131-000-youd-need-wall-to-wall-beavers-to-dam-floods/ Podcast (argument raised in OB’s interview at 3:30min ff.): https://www.dw.com/en/living-planet-beavers-triumphant-return-to-yorkshire/av-54025402 ]
- Fantastic flood demo!! Great to show the different measures to combat floods -for the percolation could you have two different "sands" with different percolation rates? Very well demonstrated and explained (smiley face). [*OB reply: yes, that can be readily arranged but we did the simple and more transportable case first.*]
- More beavers please. [*OB reply: see comment and link above.*]

14-02: Big pump breaks down. Works intermittently. Replaced on 21-02.

17-02: Small old pump breaks down; replaced on 19-02.

21-02: Replacement small pump breaks down; not yet replaced but reserve pump is providing water in upstream reservoir in sinc with the random supply of water in the moor. Galton board pretty level.

22-02: All is well but some fine-tuning, see further down for instructions.

23-02: Some fine-tuning, see further down for instructions.

Comment board (click to enlarge) and photos set-up:

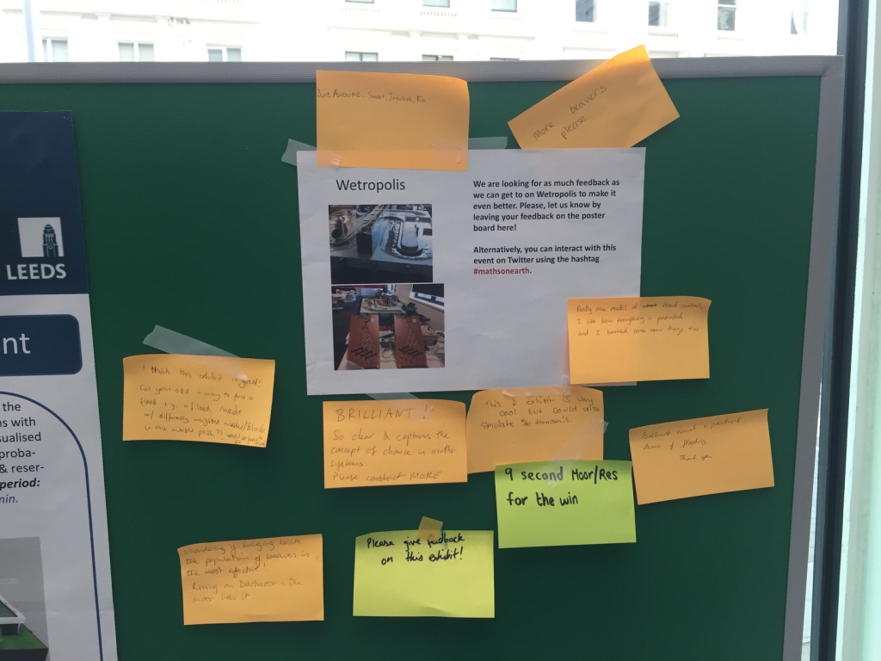
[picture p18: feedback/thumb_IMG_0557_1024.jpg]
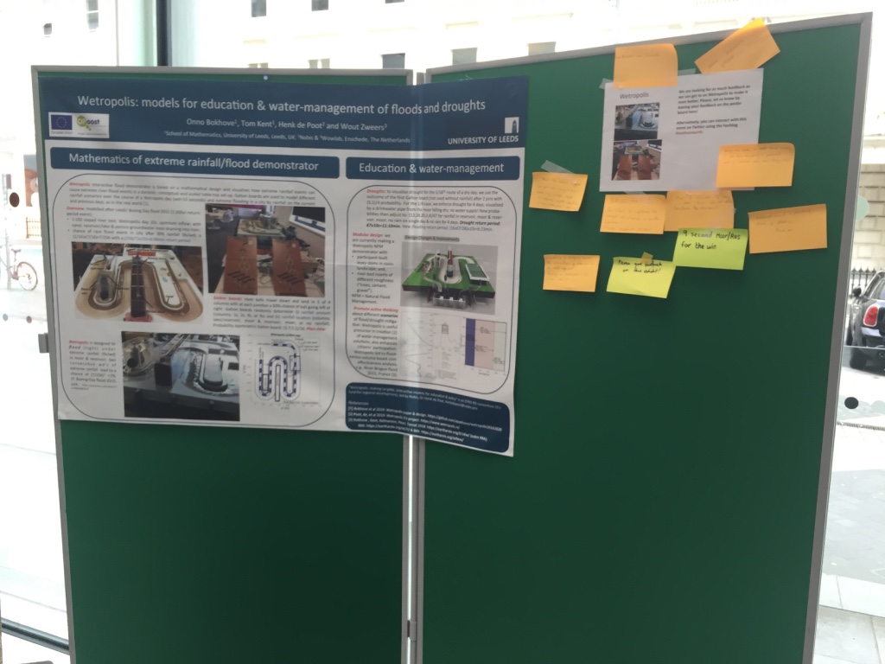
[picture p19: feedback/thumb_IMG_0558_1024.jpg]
 
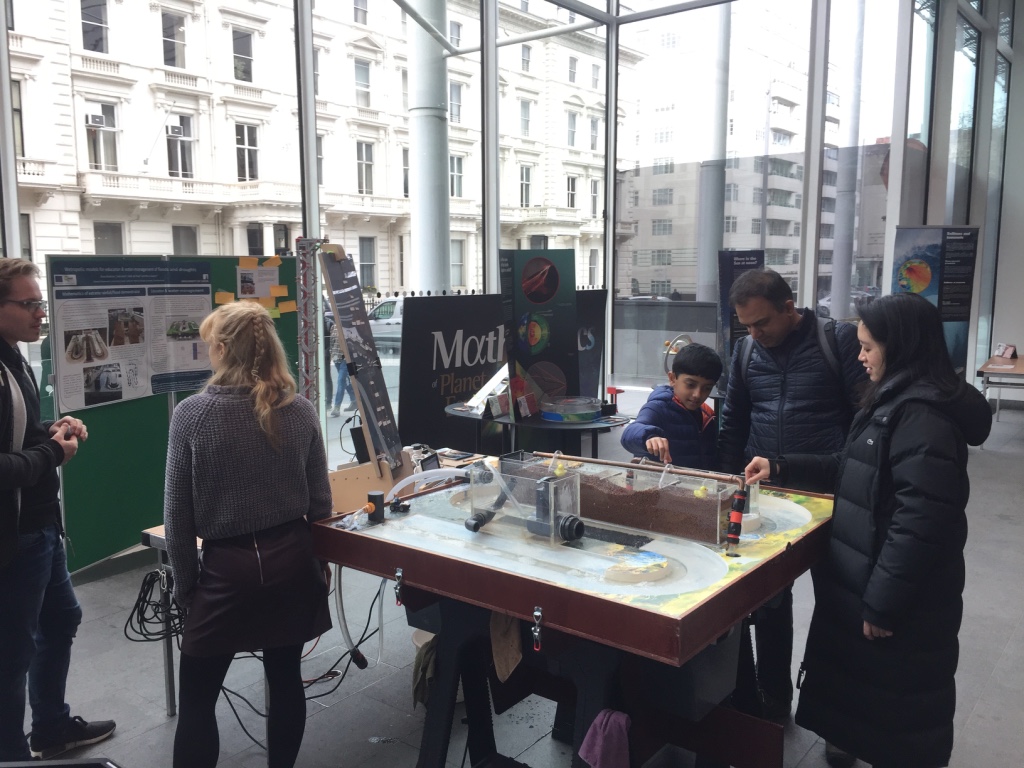
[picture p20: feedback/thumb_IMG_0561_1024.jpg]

<!-- ![PhotoC1](thumb_IMG_0557_1024.jpg) ![PhotoC2](thumb_IMG_0558_1024.jpg)
![PhotoC3](thumb_IMG_0561_1024.jpg)-->

## Instructions on how to run Wetropolis

Pointers for its smooth running on site for "wardens":
- Use the Raspberry Pi to run the serial monitor, on which one can check the collected outcomes of the two Galtonboards; if to far of and/or out of phase please check the levelness of the board with the water level. By closing and opening the serial monitor, the count starts again. Open folder on desktop (top, second/last one on right), click on Arduino file; when open click on tools and then in menu on serial monitor. E.g., on 21-02-2020 the 4th channels on (Galton Board 1) GB1 had 60 counts and GB2 had 120, while they should roughly be the same; after using the water level I saw the Galton Board was not level; I levelled it and restarted the Raspberry Pi and the count after a while was 32-32. Use: galtonboardV11march2019.ino
- Check at times whether the water level in the main reservoir is submerging the pumps; the water also cools the pumps, which otherwise burn out. Use the bucket to refill (usually half a bucket suffices).
- Check at times whether the city-overflow collection bin is full, or not, and empty when full into the main reservoir.
- A pump to the upstream reservoir can be sinced with  the moor for extra peak flow, say under climate change, this option can be turned on or off; in either case check whether 9s of rain in both moor and city reservoir leads to a flood. If not or if too much water, turn the main water supply in the top of the river down or up. Then check again.
- Check whether 9s in moor and city reservoir gives a city flood: further fine tuning is possible by loosening the clamp near the city and putting a wooden peg underneath! See fine-tuning below.
- When a duck floats in the drain to the reservoir at the end of the river it may block the pipe. So please unplug when that happens.
- There need to be four steel balls in the running; there are extra smaller ball in the grey tool bag.
- All attendants/wardens: well done, good luck and enjoy.

Extra pointers:
- Grey tool back (in one of boxes behind the scenes) contains tools.
- When an exhibition goes on longer than one (half) day, then please cover the river set-up with the blanket and the sockets and Raspberry-Pi associated with the Galton board with the bubble wrap provided.
- Bring extra replacement pumps.
- Packing up: the entire set-up fits into the back of Kia with back seats folded down.
- Make a feedback board; collect feedback given directly.

Fine tuning:
- To obtain flooding evenly in the city one needs to observe the extreme case with 9s out of 0s rain in both moor and reservoir(s); to have flow over the dike evenly, one may need to level the last bit of the set-up by loosening the clamp near the city and if nbeed be put a small wooden bit or peg between support and the Wetropolis wooden frame. See photos below. This requires "Fingerspitzengefuhl" i.e. some intuition and trial-and-error. 
- When the above does not work, more water is needed, so turn up the flow with the anlogue valves, and when there is too much flow turn them down, till you observe that it works. There is a climate-change setting, in which both more and a far-upstream reservoir are both peratig in since and a normal set-up with the upstream-reservoir not in operation, via simple swictch.

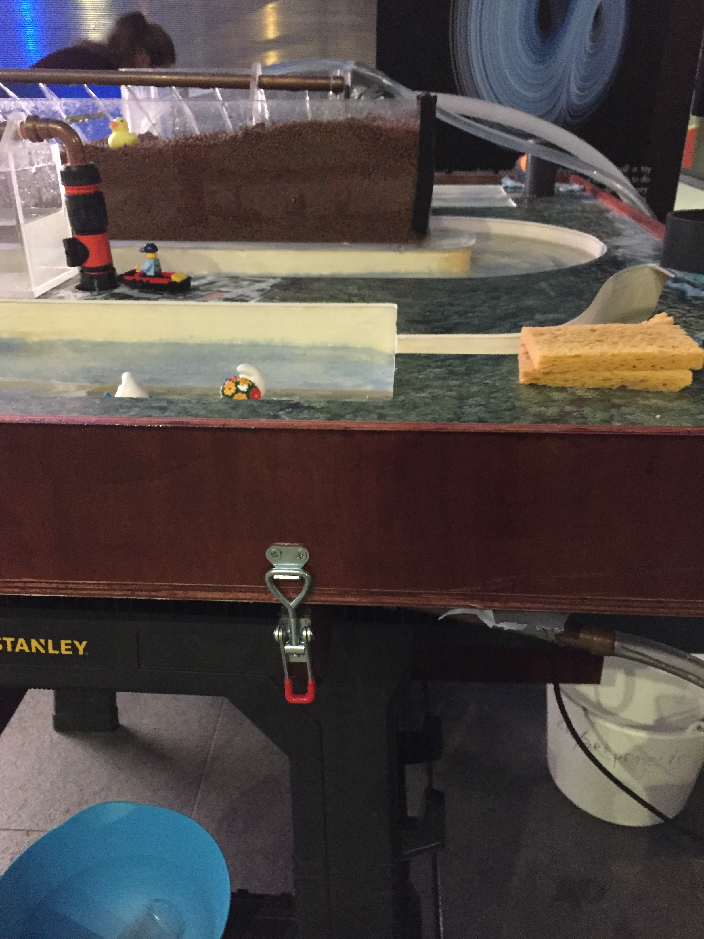
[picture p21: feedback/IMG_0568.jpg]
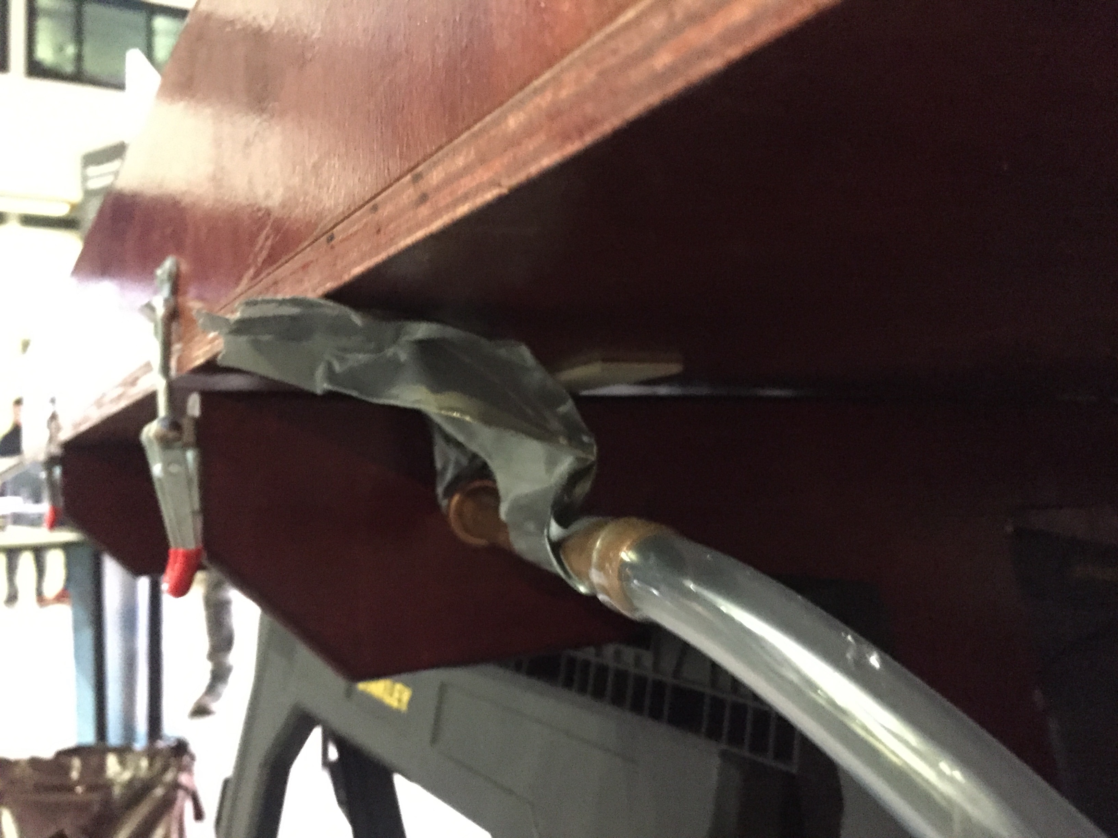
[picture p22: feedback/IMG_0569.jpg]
 

Notes, future work:
- sockets should be in one shielded box (05-2022: dones);
- extra cover on back of Galton-board set-up/marble run (05-2022 done);
- fix drainage city, use screw fittings and water collection box, with two valves (one in measurment device and one into reservoir); done 28-03 with 1 valve; balancing of drain pipe such that it is horizontal using a piece of woods is a bit sketchy; done 05-2022: added syringe with exit vcalve and drianage into reservoir
- secure drain pipes (one below seam and one at end of river); 05-2022: partially done.
- buy small toy houses;
- add switch board with several cases: normal one, climate one, extra flooding one, drought one, climate and drought and let audience analyse by observation which one is on. Do maths and progam options in Arduino (not done).
- make Arduino graphs (not done yet; see 'Just connect to your Arduino, and then go to the 'Transfer->Capture Text' menu option. Select a file to save your data and away you go! All incoming serial data will then be automatically saved for you' and https://www.circuitbasics.com/logging-arduino-data-to-files-on-a-computer/). or: https://forum.arduino.cc/t/copy-paste-problem-from-serial-monitor/694354
https://roboticsbackend.com/raspberry-pi-arduino-serial-communication/
- make matching simulations and DA etc, with associated display (in progress); and,
- buy small houses for display in the city; make/buy houses on stilts with a gangplank to higher grounds in the flood plains.

## 5. Wetropolis II:  Flood modelling and forecasting challenges in industry workshop, Sheffield, moved to 16-09-2021

Flood modelling and forecasting challenges in industry workshop https://twenty65.ac.uk/events/flood
Due to the Covid-19 pandemic, this showcasing was cancelled and, instead, Dr Tom Kent was kind enough to make and give a presentation, found here (I was preparing to and did kayak across Scotland): https://www1.maths.leeds.ac.uk/~obokhove/Wetropolis_talk_Sheffield_2021.pdf
(OB is on the committee of the EPSRC fellowship of Dr Georges Kesserwani who organised this event.)

## 6. Wetropolis II: Mathematics of Planet Earth Exhibition 28-05-2022 to 05-06 2022

Imperial College, London. https://mpecdt.ac.uk/mathematics-of-planet-earth-exhibition-2022-2/

Log:
- Arduino updating: before uploading choose board ie Arduino Mega-2560; then compile and upload
- Extended program to print histograms of top and bottom 4 channels, normalised histogram & ideal case on two lines, updated every 10s;
- Fabio (thanks, well-spotted) noticed that after 9s of rain the top Galtonboard does not count since the serial programming prevents the signal to be registered when pumoing for more than 7s; attempts to bypass this anmomaly failed hitherto; program/folder: galtonboardV11march2019c3.ino
to do: reprogram and fix the issue;
- Motor marble run failed on 02-06-2022 midday; ordered 2 new ones; likely burned out; to do; fixed 16-06 model-craft motor replaced; reserve available. 
- City: when the base is dry the water has initially difficulty rolling over the berm, once that has happened the base starts soaking up water and is slightly leaking; a fix may be to varnish one side of the city; to do;
- during transport to London the end of the aquifer collecting gutter had disappeared; fix; to do;
- during tgransport back a Mercedes car was used; everything fit in one car with the back seat folded down.
- See: https://www.lego.com/en-gb/product/loop-coaster-10303?cmp=REF-202206-Loop_Coaster_Laun

Highlights:
- the filming over 3hrs for a 3min clip; to be continued whetehr that pays off;
- two young ladies one of whom liked drowning the smurfs while the other older young lady got the hang of using flood control via the gates of the reservoir in order to protect the city from flooding, see their comments:
 

- a (French) high-school student had heard about the set-up via his brother at Imperial College and was considering using the statistics of Wetropolis for a school presentation of 3min on mathematics.

## 7. Wetropolis shown at Flood and Coast 2023 as part of Jacobs' stand
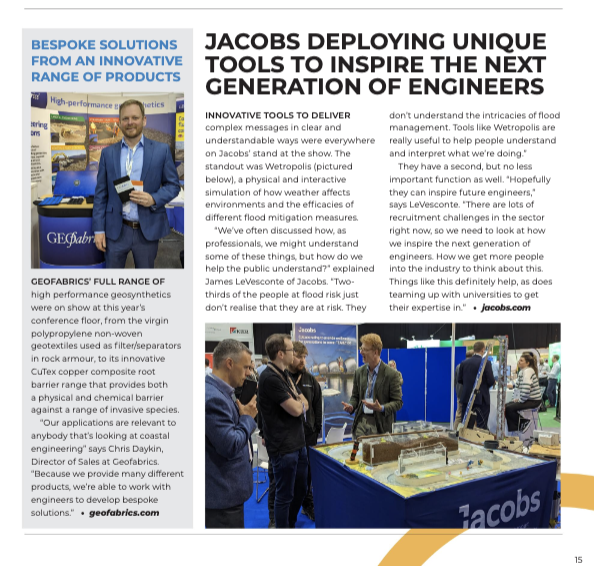
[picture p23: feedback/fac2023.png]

i.e., on p15 of: https://issuu.com/syonmedia/docs/flood_and_coast_23_showcase_ (accessed 01-12-2024).

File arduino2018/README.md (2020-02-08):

## Arduino Design Galton Board 2016, 2017 2018

There have been three Arduino set-ups:
- August 2016, here the Galton board did not work but there was a seperate option for a computerised random generator steering the two pumps for the moor and reservoir. The sketches with extension .ino are marked 2016 in the arduinofil directory. Photos pending.
- In 2017 the Arduino board with two Galton boards, including a fail-safe option using computerised steering was made; due to problems with independently steering each Servo motor the Galton boards did not work till January 2018, when OB put a wire between Servo motor of Galton Board 1 and the servo motor Galton Board 2, since the servo motor from Galton Board 2 did not seem to get any signal. These sketches with extension .ino are marked with 2017. Photos pending.
- In 2018, the Galton Boards were accompanied by a FisherTechqniue marble run brining 4 steel balls up in trun every 10s, running through two Galton Boards to create the 4x4 outcomes. Sketches are marked with 2018 or 2019. The original sketch has two errors: (i) extreme rain lasted just 7s instead of 9s (a change from 7000 to 9000 in the code) and (ii) the probabilities for the rain localisation were incorrectly assigned. This was fixed in the March 2019 sketched (further correction on 29-04-2019, uploaded), indicated as such, and marked in the file in lines with comments "Onno" and "05-3-2019" (galtonboardV11march2019.ino). Photos pending.

Design GrabCad files have extension.dxf (pdf version for direct viewing added). For instructions see the gradcad of Wout Zweers, since the files are rather large: goto https://grabcad.com/ and search for Wout Zweers; there are folders for the 2016, 2017 and 2018 designs.

Photographic overview in file (```Arduino2018pdf''') Arduino2018pdf

# Arduino design 2016 and 2017
For the 2017 and 2018 Arduino designs the  Arduino Mega-2560 has been used. The sketches are different for the 2017 and 2018 versions since pin-numbers have changed, so one cannot switche the Mega-2560 around. The pin-nummers in de GB-2016 layout correspond with names in the Arduino-2016 sketch, under variables/pins in the code with extension .ino

# Difference between 2016 en 2018: 
- In de 2018 version is the servo-motor steering for triggering the ball-releaese changed by the autonomous marble-run and in order to get a closed system, also because the servo-motors were not always working well.
-In the 2018 version uses  solid-state relais and in thee 2016 version a thread-winding relais. De solid-state relais is more trustworthy and mechanically stronger, causing less interference in the switching.

# Installation arduino on apple: 
- Currently, Arduino code uploads via the Mac-Apple are not possible (let us know if a solution has been found) because apple changed its operating system. We are now using a Rasberry-Pi and initially there were some troubles with screen size, resolved via the links below (27-03-2019). See also: https://www.raspberrypi.org/magpi/program-arduino-uno-raspberry-pi/
Changing settings for screen size of Arduino window: https://www.instructables.com/id/RUNNING-Arduino-IDE-on-RPi-800-X-480-Resolution/
Changing config.txt file: https://elinux.org/R-Pi_configuration_file

# Testing: 
- For testing, buying and using a separate Arduino is easier such that oen does not have to set up the entire installation.
- For testing with the pumps, we used two buckets with two pumps in one bucket and one in the other; keeping an eye on overflows. 
- The program test can eb done with LEDs on the pins (with 330 Ohm resistance otherwise the ports are loaded to heavily). The LEDs will signal the statues of a ports: 0 or 1 for a signal (detection of a passing object/ball) kogel) one can use 8 push-buttons, with a (10k Ohm) resistor als pull-up resistor, otherwise there is a floating port which is alternatingly or 1. [*Onno: I can't follow the previous instructions*]
- The pins can be connected directly with cables (jumping wires) or (safer and more clear) via a break-out shield. LEDs and buttons kun can be build on a broad-board, which is most straightfoward.

# List of components voor Arduino Mega: 
- Original Arduino Mega: 43,95 https://www.hobbyelectronica.nl/product/arduino-mega-2560/ or a compatible board: 11,95 euro at
https://www.hobbyelectronica.nl/product/arduino-mega-2560-ch340g-compatibel/
- Maybe a break-out for the Arduino Mega with screw-terminals: (soldered)  about 30 euro, e.g.:  https://www.ebay.com/itm/Screw-Terminal-Block-Breakout-Module-for-Arduino-MEGA-2560-R3-SKU-MD-D1236-1/202595690524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
- or (un soldered) circa 10 euro at: https://www.ebay.com/itm/1x-Prototype-Screw-Terminal-Block-Shield-PCB-Board-Kit-For-Arduino-MEGA-2560-R31/202593844266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 Take care that you order or have a small screwdriver.
- Power 6-12V 1.5A to 2A, fixed power at 12V is also okay; the power directly delievred with the Galtonboard is also okay.
- Furtehrmore, jumping wires are needed: https://www.kiwi-electronics.nl/jumperwires-kabeltjes/jumperwires-bundel
- Bread-board (or broad-board) on which one can put the buttons and LEDs:  https://www.hobbyelectronica.nl/product/breadboard-830-insteekpunten/
- Buttons: https://www.hobbyelectronica.nl/product/buttons-kleur-4-stuks/
- Resistors on the ports to protect against the LEDs from burning/too much power, or to prevent floating zeroes; (for button use) resistors at 330Ohm (one for each LED): resistors 10k Ohm (one for each button); at: https://www.kiwi-electronics.nl/Weerstand-330-ohm-1-4-watt-5-procent-10-stuks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 and https://www.kiwi-electronics.nl/Weerstand-10K-ohm-1-4-watt-5-procent-10-stuks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
- Optional: resistors 1M Ohm (for waterdepth sensor, if required, one for each pin); at: https://www.conrad.nl/p/koolfilmweerstand-1-m-axiaal-bedraad-0207-025-w-5-yageo-cfr-25jt-52-1m0-1-stuks-1417664

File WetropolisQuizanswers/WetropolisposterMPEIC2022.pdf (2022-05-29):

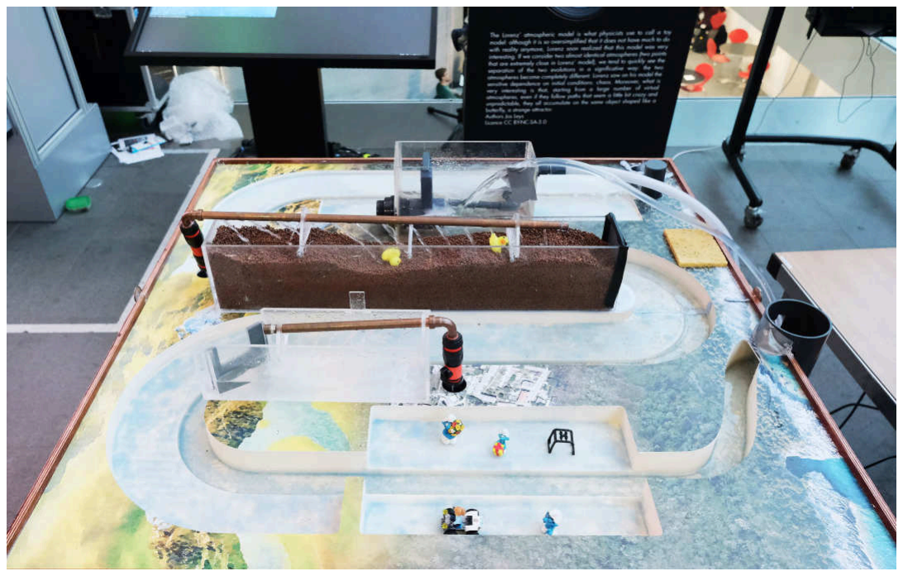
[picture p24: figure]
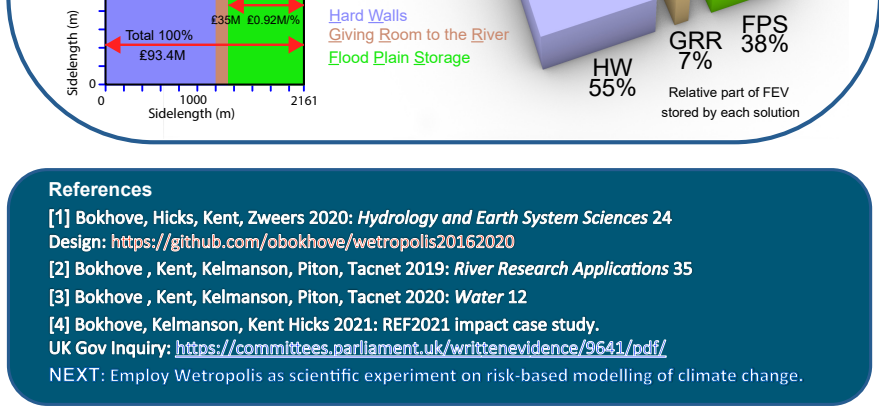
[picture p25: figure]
Relative part of FEV stored by each solution; Giving Room to the River Flood Plain Storage; 2161 Sidelength (m); Sidelength (m); Total 100% ₤93.4M; References

GRR

FPS

Discharge

Waterlevel

FEV

# Lakeside L= 2161m

Lakeside L = 2161m
2 m-deep conceptual square lake corresponding to
Flood Excess Volume (FEV)

Measures:

a) b)

c)

time

time

Hard Walls

2m depth

2161

1000

FEV = 2161² m² x 2 m ≈ 9.34 Mm³

HW 55% 1.34m

₤ 48.4M at 0.88M/%

₤10M at 1.43M/%

GRR 7%

FPS 38%

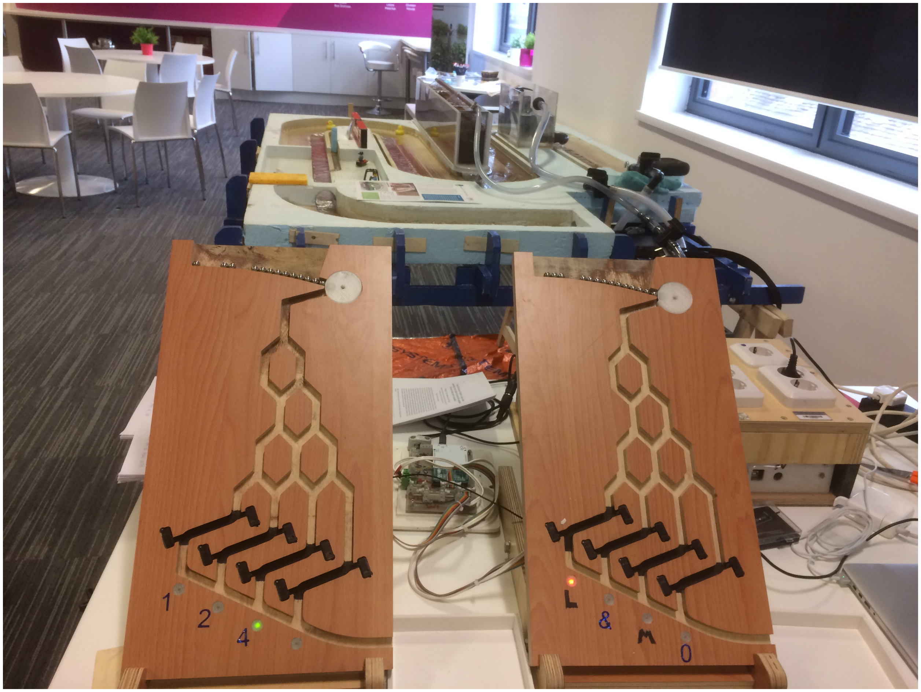
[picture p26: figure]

Galton boards: steel balls travel down and land in 1 of 4 columns with at each junc8on a 50% chance of ball going le= or right. Galton boards randomly determine: (i) rainfall amount (columns le=: 1s, 2s, 4s, or 9s) and (ii) rainfall loca8on (columns right: lake/reservoir, moor & reservoir, moor, or no rainfall). Probability asymmetric Galton board: (3,7,5,1)/16.

# Wetropolis flood and drought simulator

## Onno Bokhove, LIFD, Leeds Ins8tute for Fluid Dynamics, Leeds, UK

Mathema8cs of extreme rainfall/flood demonstrator | Showcased across UK & spin-off

Wetropolis interac8ve flood demonstrator is based on a mathema8cal design and visualises how extreme rainfall events can cause extreme river-flood events in a dynamic, conceptual, portable & scaled table-top set-up. Galton boards are used to model different rainfall scenarios over the course of a Wetropolis day of wd=10seconds that can cause extreme flooding in a city, as in the real world [1].
Overview: modelled a=er Leeds’ Boxing Day flood 2015 (with a 1:250yr
return-period event or Annual Event Probability of AEP=0.4%):
- 1:100 sloped river bed; upstream inflow; with canal, reservoir/lake & porous groundwater moor draining into the river;
- chance of rare flood event in city a=er 90% rainfall (9s/wd) is (1/16)x(7/16)=7/256 with a (256/7)x10s=6:06min return period.

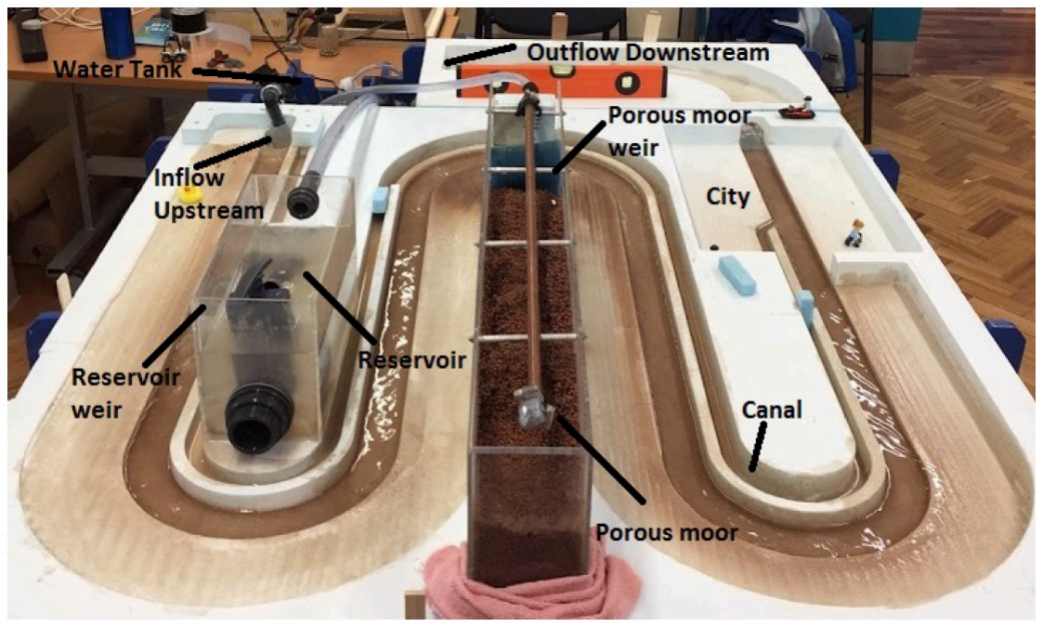
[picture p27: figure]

Wetropolis is designed to flood under extreme rainfall (9s/wd) in moor & reservoir; two consecu8ve wd’s of extreme rainfall lead to a chance of (7/256)² <1%; cf. Boxing-Day flood 2015.
See: heps://youtube.com/watch?v=N4Sp5gHXcz4
Droughts (tentative): to visualise drought for the 1/16th route of a dry day, we can use the outcome of the first Galton board (not used in absence of rainfall) a=er 2 pins with (3,1)/4 probability. For the 1/4-case, we enforce drought for 4 days, visualised by a drink-water pipe from the moor falling dry: no water supply! New probabili8es then adjust to: (12,28,20,3,4)/67 for rainfall in reservoir, moor & reservoir, moor, no rain on single day & no rain for 4 days.
Drought return period: 67x10s=11:10min New flooding return period: (16x67/28)x10s=6:23min.

Spin-off research “graphical cost-effectiveness diagnostic for policy makers” Used in EU -France and Slovenia [2,3,4]; inconvenient truths: Natural Flood Management (NFM) flood-mi8ga8on measures tend to have a small effect; flood-mi8ga8on poten8al of beavers even minute [4], despite hype (media & scien8fic) statements.

- General Assembly of Maths Foresees EPSRC network Living with Environmental Change (LWEC), Edinburgh 2016
- Leeds’ Armley Museum Public exhibi8on on Boxing Day 2015 floods 2016/2017
- Public flood conference by the Churchtown flood action group, mathema8cs of extreme events, for circa 140 flood vic8ms plus flood experts 2017
- Mathematics of Planet Earth Exhibition Wetropolis II, Imperial College 2020

### Over 1000 people experienced return periods (or AEPs) for an extreme flood by viewing Wetropolis [1] in acDon, e.g.:

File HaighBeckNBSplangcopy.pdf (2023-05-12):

Nature-based-solution for flooding, pollution and droughts of Haigh Beck
By Prof. Dr. Ir. Onno Bokhove, onnobokhove@gmail.com Apperley Bridge, 12-05-2023

Abstract
A nature-based solution (NBS) is proposed to deal with the Haigh-Beck surface-water flooding in the Apperley Bridge neighbourhood close to the River Aire, which is lying between the river and Leeds-Liverpool canal. The solution consists of separating the beck flood waters from the CSO/sewageoverflow waters, letting the then clean beck waters flow into the canal, such that a beck-flood can never reach the low-lying neighbourhood, and diverting the CSO-water via a closed 60cm diameter pipeline to the Carr-Beck-canal overflow through extra debris filters. Additional rewilding of the beck further enhances the water quality and avoiding construction, operation and maintenance of a pumping station near the river reduces our carbon footprint and localized pollution by such an industrial station. The NBS thus prevents/limits drought, pollution as well as increased rainfall threats and offers more robust protection against uncertainties/unknowns involved in extreme events.

Background, overview and challenges
Haigh Beck is a beck in the city of Bradford, UK. Haigh Beck streams from circa 150m height above sea level near the Idle Cricket Club (at what-3-words location: drives.prices.miles [0]¹
| ) to its mouth or
confluence with the River Aire (at 3-words location: among.plant.dogs) at circa 50m above sea level. Haigh Beck has a birds-eye-view-estimated length of circa 1500m, see Figs. 1 and 2. On older maps from circa 1903 and 1914, displayed in Fig. 3, it may be discerned that its source seems to lie further upstream from this cricket club, likely at “Springfield”. One observes that Haigh Beck ran past numerous mills, with several of those mills remaining to date as appartement blocks. The beck runs partially underground in culverts: a long one from Old Park Road (3-words location: cost.dish.crowned) to just NE of Robin Mills (at 3-words location: maker.eagles.royal) and a second long one from the Leeds-Liverpool canal (at 3-words location: maps.spins.vibrate) to its confluence with the River Aire next to Harrogate Road (at 3-words location: among.plant.dogs). From its reemergence NE of Robin Mills to the Leeds-Liverpool canal it runs mainly in an open, concrete channel. At that location near Robin Mills, a Combined-Sewer-Overflow (CSO), with an outflow pipe of circa 55cm to 60cm in diameter, flows into Haigh Beck, see the photo in Fig. 4 (at 3-words location: maker.eagles.royal).

At the Dyehouse Mill near the canal (at 3-words location: divide.undulation.jets), there is a an old splitter-gate (next to the existing Dyehouse Mill marked in Fig. 3; at 3-words location: riots.total.handle), dividing the combined CSO-beck flow:
(a) either into an open channel of circa 20m to near the canal and then in a culvert under the Leeds-Liverpool canal and further underground to its mouth into the River Aire, or
(b) via a wider open channel-bed into the Leeds-Liverpool canal, or via both routes.
The splitter-gate is locked and seems to be operated by the Canal-and-River Trust.

Intermittently, beck water is adjusted to flow into the canal as one can sometimes observe from the canal or its tow path. Intermittently, the CSO flows into the beck. At high levels of CSO-beck waters, the splitter-gate cannot handle the flow rate and CSO-beck waters (over)flow into both culvert and canal (as shown in footage on 20-10-2022 on the Facebook page of Friends-of-Bradford’s-Becks (FoBB) and OB’s YouTube channel [4]).

Since 1903, the following housing developments emerged:
i. next to the River Aire between the canal and river with Fig. 3 revealing older dwellings and a hotel at this location; and,

1 References are found near the end of this document and indicated by [0], [1], etc.

ii. the 1980’s/1990’s Apperley Bridge neighbourhood South of the Leeds-Liverpool canal, including the converted mills (see Fig. 3 with the named Dyehouse Mill, Valley Mill and Canal Mills).

Around 2000, local flooding of Haigh Beck in the late ‘90’s over and at the current Tenterfields road, involving various houses between the beck and the Apperley Bridge marina, was solved by building a modern culvert (at 3-words location: roofs.lines.circle) with grating holding back debris (source: online newspaper article [5]). The debris has been regularly cleared by council, as well as by local citizens who noticed it is or was not cleared sufficiently often.

The houses along the entire culvert North of the canal have faced intermittent flooding of cellars and gardens with polluted CSO-beck waters over two to seven (or more) decades due to culvert collapse, blockages and such. Also, the outflow of CSO-beck waters into the river is blocked at higher River Aire levels, due to a valve which automatically closes, even at intermediately high River Aire levels. In that case the houses along the beck culvert can flood from the combined CSO and beck waters without the River Aire levels flooding these properties. The reason is that the CSO-beck waters have sunk to a level that is too low relative to some river levels once the beck has crossed the Leeds-Liverpool canal. An obvious solution is to let clean beck waters flow into the canal, such that these do not reach levels too low to require pumping. The Leeds-Liverpool canal has several wide overflows towards the river to deal with excess canal water, notably one circa 200m east of Dyehouse Mill (i.e. at 3-words location: riots.total.handle), where it joins the Carr-Beck culvert under the canal, and circa 3 miles downstream along the Leeds-Liverpool canal at Rodley, and a further 4.5 miles downstream at the Newlay Three Rise Locks at Brambley. Several instances of surface flooding North of the canal in Apperley Bridge have been filmed and reported since 2020. Both in person and online, locals have reported decades of intermittent surface flooding by CSO-beck waters, again noting that surface flooding can occur when intermediate-high River Aire water levels close off or block beck flow into the River Aire.

In summary, the following challenges posed by the combined CSO-beck flow have arisen in the last few decades:
A. Surface-water CSO-beck flooding along the Haigh Beck culvert in the Apperley Bridge neighbourhood between canal and river, for which emergency services have been called in numerous times to pump away the polluted CSO-beck flood waters. A new pumping station has recently (2022- January 2023) been proposed with storage space and additional culverts, given that new FAS-II flood-defence walls along the River Aire will further trap CSO-beck waters and induce flooding from within these new flood-defence walls [1]. Unresolved issue.
B. Pollution, odours and rat infestations in the neighbourhood South of the canal and the neighbourhood North of the canal along the Haigh Beck, due to and downstream of the Haigh Beck CSO. Unresolved issue.
C. Climate-change induced intense rainfall causing future flooding in the neighbourhood North of the canal, dealing with “known unknowns and unknown unknowns” [6,7]. Unresolved issue.
D. Drought in the canal during (climate-change enhanced) drought periods. Unresolved issue.
E. Deposition of solid debris, including wet wipes, sanitary pads and such along the beck downstream of the CSO. Such solid debris over years is found in heaps next to the beck culvert under Tenterfields Road (at 3-words location: roofs.lines.circle). Unresolved issue.
F. The short, somewhat hidden circa 20-m open channel of Haigh Beck along Dyehouse Mill is a danger to life since animals and humans can fall in and be sucked into the culvert under the canal during high flow rates (see 20-10-2022 footage on OB’s YouTube channel [4]), since it is uncovered. Unresolved issue.
G. Due to both the CSO and the beck flowing in a concrete channel, natural life within the beck is minimal downstream of the CSO flowing into Haigh Beck. Further issues hampering natural life are the strong ochre-content of the beck (see Fig. 5) and known and unknown storm drains with misconnections. One storm drain with a misconnection flows into Haigh Beck in the beck South of Old Park Road (roughly at 3-words location: loaded.evenly.them), see Fig. 6. Unresolved issue.

Proposed nature-based solution (NBS)

Challenges A-to-G can be readily resolved by combining two measures, based on the main principle that CSO-beck waters should not enter the low-lying flood-prone area between canal and river, in combination with rewilding the beck:

(i) By avoiding the CSO to overflow into the beck via the construction of a separate declined pipeline (diameter 55cm to 60cm) from the current CSO to the canal and then via another declined pipeline (diameter 55cm to 60cm) leading CSO waters along (in/above) the South side of the canal till under and past Harrogate road and then along (in/above or onshore-next-to) the canal to the Carr-Beck overflow (at 3-words location: party.jazzy.grew); and,
(ii) By letting the new clean, no longer CSO-polluted, Haigh Beck waters flow into the canal, using the existing wide channel and noting that excess canal water has existing and automatic overflows in Apperley Bridge and Rodley to the River Aire, and downstream to the next canal segment.
(iii) By rewilding of the beck at least at two spots downstream of the current CSO:
(a) Wildlife in Haigh Beck downstream of the CSO can be enhanced by breaking through the vertical concrete side-wall on the NW side just upstream of the Tenterfield grating at the depression on the park side (i.e., at 3-words location: equal.frame.quit). Meandering can be enhanced by placing obstacles in the flow. By preserving the East wall (and bottom) of the concrete channel, channel erosion on that side will be prevented. Similarly, erosion on the Western, park side can be avoided by introducing stone shores or steps, thus limiting erosion due to dog access. Such reintroduction of a meandering beck also will increase flood-water storage. Keeping one side of the concrete wall prevents erosion of the steep slopes.
(b) Opening the shores on the East side of the beck into the low-lying area between the current CSO exit and the path via one dam or more leaky dams in the larger private-property area will enhance wild-life and flood storage (i.e., at 3-words location: sides.violin.undulation).

Remarks:
- Note that solution (i)-(ii) exclusively uses gravity to drive the flows, naturally, with no pumping station required, using the design principle that the CSO-beck water should never enter the low-lying area between canal and river which often requires pumping or causes local surface flooding. The solution (i)-(ii) would have been easiest to implement before the neighbourhoods at the river and just south of the canal were built circa 70 and 30 years ago²
. Avoiding construction, operation and maintenance of a pumping station near the River Aire reduces our carbon footprint and localized pollution by such an industrial station.
- Note that another proposed solution by Mott MacDonald/Bradford City Council involving a pumping station, storage tanks and more culverts [1] near the River Aire requires long-term maintenance and energy use, and only deals with challenge A, and not with any of the other identified challenges B-to-G. The solution of Mott MacDonalds/Bradford City Council thus appears to be more expensive, involves more maintenance, and is less sustainable and climate-change resilient, and is less able to deal with “known and unknown unknowns” [6,7]. It does not use a holistic approach considering the entire Haigh-Beck catchment, in contrast

2 The suggested solution was inspired by Robert Hellawell’s comment that in modern neighbourhood a concrete channel for combined CSO-beck flows would no longer be permitted.

to the proposed NBS-approach, which builds on earlier and reported suggestions made in 2021.
- The pumping station is mainly required because the high volume of CSO-beck waters reaching the low-lying area between canal and river, with flows over 1m³
/s mentioned for
two hours [1], which equals a volume or reservoir of circa 85x85x1m³ after two hours.

(iv) To deal with potential siltation of the canal by inflowing beck waters, a siltation screen can be placed, either in the canal or in the wide inflow channel, or both, such as to avoid or limit dredging of the main canal channel.

CSO-pipeline construction options and estimates of construction timeline
Various options for the CSO-pipeline to the canal and along the South side of the canal to the Carr-Beck overflow can be considered (see Fig. 7, red line indicating the pipeline):
- South of the path from the CSO to the path a pipe of matching diameter is dug into the soil on the East side of the beck, crosses the beck with its culvert under the path and continues between beck and path dug into the soil toward the Tenterfields culvert.
- Alternatively, the pipe gets laid under and into the floor of the beck, of which there are examples in other cities.
- At the culvert under Tenterfields road (at 3-words location: equal.frame.quit) the pipe is put into the existing culvert, i.e. within the pipe separated from the beck waters, since it has been designed to have ample space for both beck and CSO waters.
- Depending on the size of the culvert to the splitter-gate the pipe continues in the culvert or a separate trench is dug along the edge of the car park for the CSO pipe.
- The splitter-gate is modernised with the pipe continuing to the canal using the space of the current open channel directly adjacent to Dyehouse Mill.
- The existing culvert at Dyehouse Mill and its passage under the canal are closed off.
- The pipe continues at the edge of the canal till past Harrogate Road where it either is cut through the canal border and continues in a trench dug into the existing green strip or it continues along the edge of the canal to the Carr-Beck overflow, to finish into Carr Beck with its intermittent Greengates-CSO waters.
- There are several pipe options: concrete, steel or light-weight plastic/PVC.
- The entire pipeline is laid under a (slight) decline such that no pumping station is required since the flow is thus gravity driven.
- Clean-up consist of water being flushed through the pipes, driven by gravity. Additional filtering or screening at the Carr-Beck overflow can be used to catch solids, since there is some space with a larger vertical drop. Note that the current CSO does regularly release solids, as evidenced by heaps of debris in the concrete beck channel (e.g., see Fig. 4), next to the channel at the Tenterfields culvert-grating (at 3-words location: equal.frame.quit), the entire concrete channel and in the existing wider beck channel flowing into the canal at Dyehouse Mill.

21st-century future extensions

(a) Modernisation of the sewage network in Haigh Beck catchment by splitting rainfall drainage from sewage drainage will diminish or eliminate CSO releases. An emergency CSO will remain necessary to avoid sewage entering homes in emergency situations but the latter emergencies can be reduced.
(b) BBC Futures highlights novel yet already existing treatments of sewage at in-situ micro-plants, which could become a way of dealing with sewage and is already in use in some various cities [3].

Questions

- There do not seem to be data or estimates thereof made available on the volume of beck water and the volume of CSO-water released during higher water levels.
- Data of volume estimates of each release of the Haigh Beck/Stockwell CSO over the years are required, e.g. in 2021 and 2022 have not been made available by Yorkshire Water, despite FOI requests and despite Yorkshire Water’s open data policy. Such data are relevant to estimate expected CSO flow rates, in order to use these in any design.
- Total existing combined CSO-beck water flow rates are stated in the Mott-MacDonald/Bradford City approach at a maximum of 1.53 m³

/s with CSO-beck discharges above 1.0m³ /s for over two
hours in certain scenarios, with a peak flow pump action at 0.245 m³
/s required, possibly over 5 to 10 hours [1]. The pumps are also required to alleviate locally trapped rainfall amounts.
- Note that two hours of flooding at 1.0m³
/s concerns a volume of 7200 m³ (2 hours being 2x3600s), equating to a lake or reservoir of circa 85x85x1m³
. Note that the quoted [1] 10 hours of pumping at 0.245 m³

/s concerns a volume of 8820m³ (10 hours being 36000s), equating to a lake or reservoir of circa 94x94x1m³
. These are substantial volumes caused by the CSO-beck water flowing into the area between canal and river during intense rainfall events, which fact triggered the NBS-approach principally avoiding those waters to flow into that low-lying area and hence avoid pumping to be required. (The data of Table 3 in [1]b should preferably be displayed graphically and the cumulative volume per case calculated, for clarity’s sake.)

References
[0] https://what3words.com/
[1] (a) Main site with planning documents: https://planning.bradford.gov.uk/online-applications/applicationDetails.do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
(b) In particular document (Table 3):
https://planning.bradford.gov.uk/online-applications/files/D647059F07FAA8715E84FCCB1018042E/pdf/21_00249_SUB04-COMPARISON_OF_POST_SCHEME_AND_BASELINE_PEAK_FLOOD_LEVE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
mentions engineered solution with pumps, while the NBS-solution avoids the entry of CSO and beck waters South of the canal altogether.
[2] Friends of Bradford Beck (FoBB): https://www.facebook.com/groups/BradfordsBecks
[3] The secret science of sewage. https://www.youtube.com/watch?v=D6HnBQ-qJMA
[4] YouTube channel: https://www.youtube.com/user/onnobokhove
[5] https://www.thetelegraphandargus.co.uk/news/8065424.estate-may-see-breakthrough-in-long-battle/
[6] Poortvliet et al. 2019: On the communication of statistical information about uncertainty
in flood risk management. https://www.sciencedirect.com/science/article/abs/pii/S0925753518309755
[7] Di Baldasarrre et al. 2014: On the communication of statistical information about uncertainty in flood risk management.
https://www.tandfonline.com/doi/full/10.1080/02626667.2015.1091460

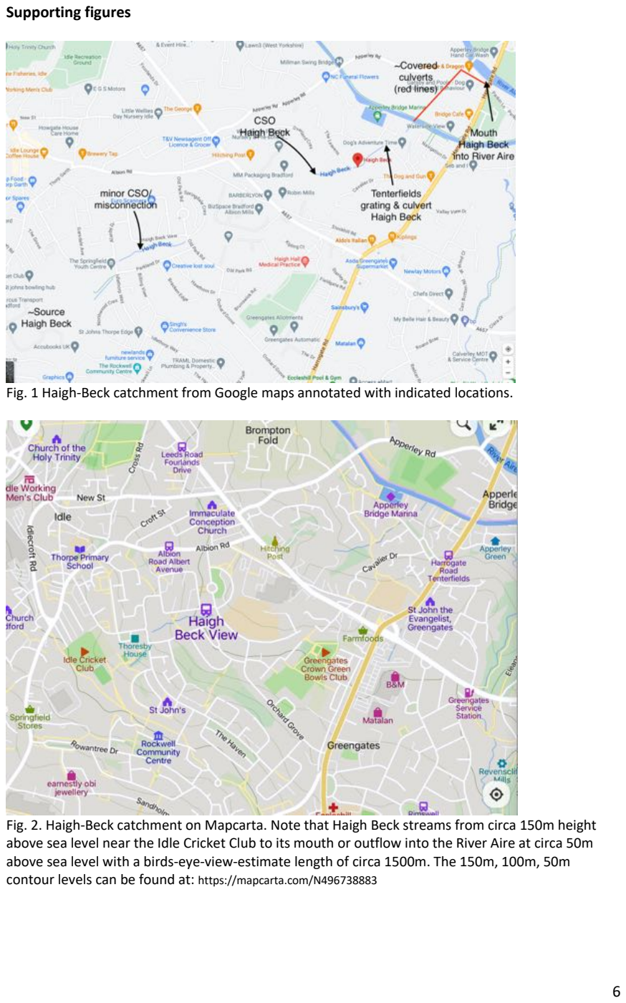
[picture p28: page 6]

Supporting figures

Fig. 1 Haigh-Beck catchment from Google maps annotated with indicated locations.

Fig. 2. Haigh-Beck catchment on Mapcarta. Note that Haigh Beck streams from circa 150m height above sea level near the Idle Cricket Club to its mouth or outflow into the River Aire at circa 50m above sea level with a birds-eye-view-estimate length of circa 1500m. The 150m, 100m, 50m
contour levels can be found at: https://mapcarta.com/N496738883

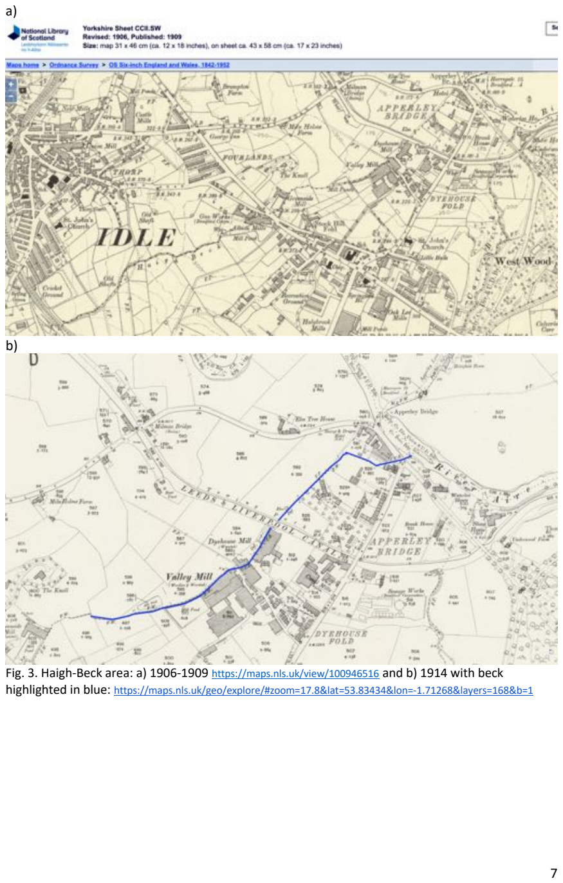
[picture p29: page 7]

a)

b)

Fig. 3. Haigh-Beck area: a) 1906-1909 https://maps.nls.uk/view/100946516 and b) 1914 with beck
highlighted in blue: https://maps.nls.uk/geo/explore/#zoom=17.8&lat=53.83434&lon=-1.71268&layers=168&b=1

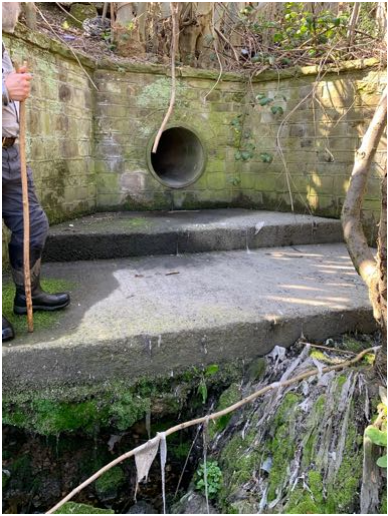
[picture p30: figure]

Fig. 4. Combined-sewer-overflow (CSO) permit number 1862 of Haigh Beck with CSO-debris (rags and wet wipes) on the foreground. "Stock Hill Fold No 2 Cso (Yorkshire Water)”; “In 2021, this sewer storm overflow spilled 45 times for a total of 174 hours, discharging into the Haigh Beck”; “In 2022, this sewer storm overflow spilled 36 times for a total of 64.92 hours, discharging into the Haigh Beck”, sewage map: https://theriverstrust.org/sewage-map Photo OB 08-04-2023.

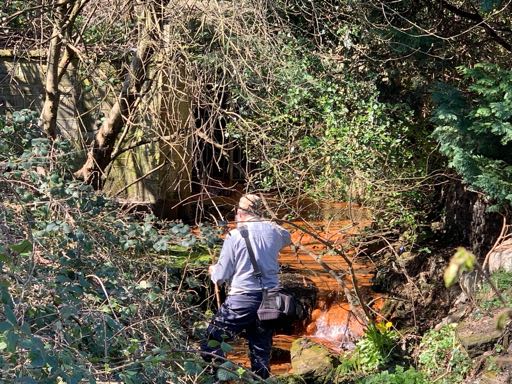
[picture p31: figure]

Fig. 5. Ochre-coloured waters of Haigh Beck near the CSO (at 3-words location: maker.eagles.royal)). The low water quality on 08-04-2023 was apparent since “the absence of certain pollution sensitive families of aquatic invertebrates, such as upwinged flies, and the abundance of invertebrates which are more pollution tolerant, such as freshwater hoglouse, is indicative of low water quality"; in addition: “the ochre found in the stream, whilst naturally occurring, is also a serious pollutant and will be detrimental to the water quality” (Robert Hellawell). Photo OB 08-04-2023.

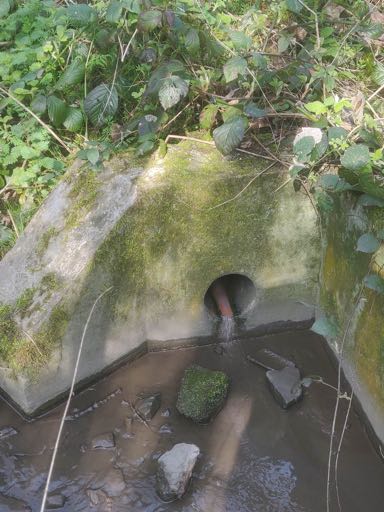
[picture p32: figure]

Fig. 6. Surface-water storm drain with misconnection into Haigh Beck, North of Old Park Road (at 3-words location: loaded.evenly.them) during a dry day. “It is [likely] a surface-water drain into which a sink, shower, bath or dishwasher has been misconnected: http://www.connectright.org.uk/“ (Robert Hellawell). Photo courtesy: Barney Lerner, taken during the FoBB clean-up on 08-04-2023.

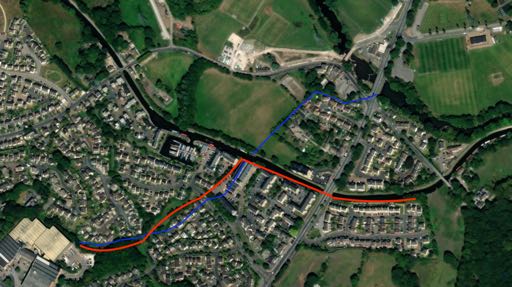
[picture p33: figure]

Fig. 7. Haigh Beck ~1900 course overlaid in blue and prospective CSO-pipelines overlaid in red on google maps.

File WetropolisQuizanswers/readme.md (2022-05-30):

# Wetropolis Flood Demonstrator Quiz: questions and answers

## Welcome to the Wetropolis Quiz on extreme rainfall and river flooding! Work together?

Q1: How long does it (approximately) take for the steel ball to fall through the Galtonboard(s)?

a) 1 second; b) 10 seconds; or, c) 100 seconds?

That is the length of a day in Wetropolis, a Wetropolis day —with new SI unit wd.

ANSWER: b) The Wetropolis day or wd is 10 seconds.

Q2: Notice which two lights light up on the Galton board(s) during a wd (Wetropolis day)and notice what happens in the river set-up with rain falling on the moor and reservoir.

When the lights in channels “2 seconds” and “moor” lit up, what happens in the set-up?

a) Rain falls for 4s in the reservoir; b) there is no rain; c) rain falls for 2s in the moor. 

ANSWER: c) Rain falls for 2 seconds in the moor (the box with the porous particles representing a porous peat moor, say).

Q3: There are 4 rain duration outcomes (that is: 1s,2s,4s,9s of rainfall per wd) and 4 rain location outcomes (that is: rainfall in reservoir, in reservoir & moor, in moor, no rain).

What is the most extreme rainfall event possible during one Wetropolis day?

a) No rainfall; b) 9s in moor; c) 9s in reservoir & moor; d) 9s in reservoir.

Locate the city in the set-up. Next observe Wetropolis over several Wetropolis days and notice that the city (only) starts to flood after such an extreme rainfall event. On average you will have to wait for a certain number of Wetropolis days, the return period, for flooding to occur.

ANSWER: c) 9s of rainfall in both the reservoir and moor.

Q4: When an extreme event is seen to occur aftre a steel ball falls through the Galtonboard(s), what can you do the lessen or prevent the city from flooding?

a) Hold back water in reservoir by using its lock gates; b) nothing; c) hold back water in reservoir by using lock gates after first (sufficiently slowly, why?) emptying it during “dry” times.

ANSWER: c) By first emptying the reservoir without flooding the city during sufficiently dry Wetropolis days one can create more volume in the reservoir to store rainfall, but only till the reservoir is full. So answer c) is better than answer a).

Q5) During climate change more (annual or Wetropolis) rainfall is predicted. Find the climate-change rainfall switch; turn it on and observe what happens.

ANSWER: See the red switch sticking out of the wooden lid.

Q6: The water volume that floods the city is the flood-excess volume: collect and measure that volume underneath the city by turning the valve off/on under the city (and play!)

The Wetropolis Event Probability (WEP) is thus circa 2.73%, the analog of the Annual Event Probability (AEP used by the Environment Agency in flood-risk maps for your house. The EA uses 1/30=3.3%, 1/100=1% and 1/1000=0.1% flood-risk thresholds -see https://check-long-term-flood-risk.service.gov.uk/postcode

Q7: In the ideal case of 50%-50% splits on the Galtonboard, what is distribution in the 4 Galtonboard channels?

Hint: first split 1/2 & 1/2; 2nd split: 3/4 & 1/4; 3rd split: 3/8 & 1/2 & 1/8; final split and answer: 3/16 & 7/16 & … & 1/16.

Answer (see poster): 3/16 & 7/16 & ... & 1/16.

ANSWER: 3/16 & 7/16 & 5/16 & 1/16 (on average).

Q8: How often does such an extreme rainfall event occur? What is its chance of occurrence?

a) 1/16 x 7/16=7/256; b) 1/16; c) 5/16x5/16=25/256; d) 7/16x1/16=7/256. (See poster.)

ANSWER: a) 1/16 x 7/16=7/256;

Q9: Extreme rainfall occurs circa 3% (2.73% to be more precise) of the time on average.

What is then the return period for such an extreme flood event?

a) 256/7~36wd’s or 6:06min; b) 120wd’s or 20min; c) 16wd’s or 160s. (See poster.)

ANSWER: a) 256/7~36wd’s or 6:06min with 36x10s=6min.

Q10: How do the two Galtonboard distributions approximate their ideal distributions?

Answer: see the outcome (updates) on the Raspberry Pi (move the mouse and look at the serial monitor; printed lines with numbers per channel, normalised and ideal outcomes). What can we do to improve the outcomes?

Q11 (bonus question): What is the chance that a Wetropolis superflood occurs, i.e. what is the chance of 2 wd’s of extreme rainfall?

ANSWER:  (7/256)*(7/256)=0.075% or after on average 1337wd's, which is 3:43hrs, a long time to wait (on average). We saw 2 superfloods on 29-05 in an 8hrs period. See movie: https://www.youtube.com/shorts/pgQMljCGl6o

Poster: https://github.com/obokhove/wetropolis20162020/blob/master/WetropolisQuizanswers/WetropolisposterMPEIC2022.pdf

Comments? o.bokhove@leeds.ac.uk

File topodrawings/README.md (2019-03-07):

## Topography of landscape 

# Topography design files 2016, 2017-NFM and 2018
There are currently design files for the topography of:
- the Augusts-2016 version, marked 072016, 082018 or aug2016feb2017; see also https://workbench.grabcad.com/workbench/projects/gcei8hHYFSUXwaASLHjilw8E6iDf7C9ZUmoHGAatrqLrAw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
- the 2017 Natural Flood Management (NFM), marked 2018NFM; see also: https://workbench.grabcad.com/workbench/projects/gciPLkWlkyCXN4i54EdjmGzpnj2zUENcm5J4qKWmBu20Tf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
- the 2018 Natural Flood Management (NFM), marked 2018NFM; see also: https://workbench.grabcad.com/workbench/projects/gccv9PkptEUUEtIWc2rthwbslBnbWa_9fVAP7_x9OyM65N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

The procedure to use these in autocad and set up the routing is explained in under the grabcad links above.

# Protocol and check second NFM-Wetropolis topography
Monday 04-03-2019 Hand-measurements of mid-channel slope of polystyrene topography 2017 Wetropolis NFM plates. Using a simple handruler after levelling the set-up with a horizontal level, for both the foam-bounding box and the fitted foams themselves. The ruler has an offset H=(0.7+-0.1)cm. It is better to use a caliper and, if possible also, a dumpymeter to check the topography routed in the foam block but the use of a ruler suffices as a first check of anomalies.

| Point | height (cm) +-0.1cm | slope estimated | comment |
|---|---|---|---|
| 1 | H+1.3 |-| 0.02m from inflow circle | 
| 2 | H+1.8 |0.0179 | 0.3m from inflow point | 
| 3 | H+2.05| 0.0083  | 0.6m from inflow point | 
| 4 | H+2.2 | 0.01 | 0.75m from inflow point | 
| 5 | H+2.4 | - | middle 1st bend | 
| 6 | H+2.6 | - | past pt opposite to 0.75m pt 4| 
| 7 | H+3.3 |- | oppositie 0.2m from inflow pt | 
| 8 | H+3.5 |- | arc 2nd bend | 
| 9 | H+4.0 | - | opposite 0.2m from inflow pt & pt 7 | 
| 10| H+4.3 |0.01 | 0.3m downstream from pt 9 | 
| 11| H+4.5 | 0.0067 | 0.6m downstream from pt 9 | 
| 12| H+4.9 |- | arc 3d bend | 
| 13| H+5.1 |- | opposite 0.6m downstream so of pt 11 | 
| 14| H+5.25 |0.0094 | entrance city 0.16m downstream from pt 13 |
| 15| H+5.55 |0.0071 | end city 0.42m downstream pt 14 | 
| 16| H+5.65 |- | middle straight of exit bends |
| 17| H+6.8 | - | exit |

In conclusion, the slope of the main channel is pretty close to 1:100. Overall drop is 5.5cm over 4.2 or more meters, which is about a 0.0131 slope. I forgot to measure the overall length of the channel with a string. 

**_Quality-control protocol_**
A quality-control protocol is therefore:
- Qua1: level the polystyrene foam blocks in their actual setting with a horizontal level, both the foams and a bounding box, if any.
- Qua2: relative to the top of the foam, assumed flat, please check, measure the depth of the main river channel from source to sink and check whether the measured slopes match the design slopes.
- Qua3: repeat with caliper, if there is reason to do so.
- Qua4: repeat if possible with a dumpymeter, if there is reason to do so.

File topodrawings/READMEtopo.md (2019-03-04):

Monday 05-0-2019 Hand-measurments of mid-channel slope of polystyrene topography 2017 Qetropolis NFM plates

Using a simple handruler after levelling the set-up with  a leveler, of both the box and the foams.

| Point |  height (mm) +-1mm |  comment |
----------------------------
| 1 | 1.3 | 0.02m from inflow circle |
| 2 | 1.8 | 0.3m from inflow point |
| 3 | 2.05 | | 0.6m from inflow point |
| 4 | 2.2 | 0.75m from inflow point |
| 5 | 2.4 | middle 1st bend |
| 6 | 2.6 | past ar opposite to 0.75m pt 4|
| 7 | 3.3 | oppositie 0.2m from inflow pt |
| 8 | 3.5 | arc 2nd bend |
| 9 | 4.0 | opposite 0.2m from inflow pt & pt 7 |
| 10| 4.3 | 0.3m downstream from pt 9 |
| 11| 4.5 | 0.6m downstream from pt 9 |
| 12| 4.9 | arc  3d bend |
| 13| 5.1 | opposite 0.6m downstream so of pt 11 |
| 14| 5.25 | enttrance city 0.16m downstream from pt 13 |
| 15| 5.55 | end city 0.42m downstream pt 14 |
| 16| 5.65 | middle straight of exit bends |
| 17| 6.8 | exit |
--------------------------------

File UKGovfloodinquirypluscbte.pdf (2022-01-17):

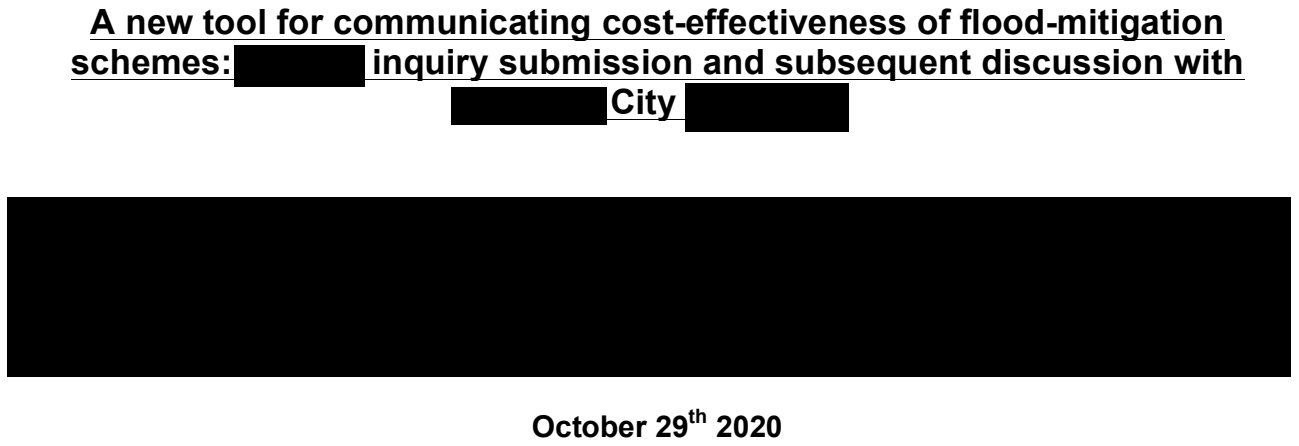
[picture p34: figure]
Leeds City Council; Onno Bokhove¹; , Mark Kelmanson¹; , Tom Kent¹; Leeds LS2 9JT, W. Yorks., UK; France; October 29th 2020

### A new tool for communicating cost-effectiveness of flood-mitigation schemes: DEFRA inquiry submission and subsequent discussion with

, Guillaume Piton² and Jean-Marc Tacnet² 1 School of Mathematics and Leeds Institute for Fluid Dynamics (LIFD), University of Leeds,

2 Univ. Grenoble Alpes, INRAE, UR ETGR, Centre de Grenoble, F-38402, Saint-Martin-d’Hères,

Resumé This document is an amalgamative overview of materials emerging from both work on a new flood-mitigation protocol conducted by the authors since 2017, and recent discussion thereon with its targeted beneficiaries at Leeds City Council.

- Part 1 of the following comprises the verbatim text of a September 2020 submission by the authors to an ongoing DEFRA committee inquiry into flooding.
- Part 2 is a discussion (October 2020) of Part 1 in the form of the authors’ point-by-point responses to verbatim comments by the senior flooding engineer at Leeds City Council.
- Part 3 is a graphical overview of the authors’ protocol that augments Figure 1 of Part 1 in both a quantified and visually striking way.

Part 1 : Environment, Food and Rural Affairs Committee inquiry into flooding

Submission: A new tool for communicating cost-effectiveness of flood-mitigation schemes

Summary:

- The “Wetropolis” flood-outreach demonstrator has been developed at Leeds to enable live visualisation of so-called return periods of extreme rainfall and flooding events to the general public.
- A team of Leeds mathematicians and French civil engineers has developed a novel and innovative way of visualising and analysing complex flood-protection schemes.
- This protocol, or tool, has been designed with the express intention of empowering decision-makers and flood action groups, as well as the general public, to make quantified judgements on the cost-effectiveness of flood-mitigation plans in order to facilitate enhanced evidence-based decision-making. The tool enables rapid a priori, as well as thorough a posteriori, comparisons to be made of various flood-mitigation options and scenarios.
- To date, the tool has highlighted that, in contrast to media promulgation, the effectiveness of Natural Flood Management (NFM) in the mitigation of medium- to large-size floods is small, if not minute. For example, at least 8500 beaver colonies — an unrealistic and unattainable upscaling — would be required to mitigate the notorious Boxing Day 2015 floods in Leeds.
- The tool is, however, objective, and so could equally highlight that for certain floods – i.e. sufficiently small and localized, with a “flood-excess volume” (see section 1.2 below for definition) of less than ~10,000 cubic metres, one beaver colony could potentially mitigate ~20% of the damage, with the remaining ~80% needing to be absorbed by other flood-mitigation measures.
- Hence, referring to the ToR, the new tool demonstrably addresses how “communities can be involved most effectively” [ToR#4] in flood mitigation, how “increasing focus on natural flood management measures” [ToR#5] has to be put in an evidence-based context of being predominantly relevant for the mitigation of small-scale floods, and how “lessons can be learned from the recent winter floods” [ToR#7]. We subsequently refer in bold, with accompanying reasons, to where [ToR#3, ToR#4, ToR#5, ToR#7] are relevant in the main text.

Researchers involved:

- The work is a collaboration between applied mathematicians Professor Onno Bokhove, Professor Mark Kelmanson and Dr Tom Kent from the School of Mathematics at the University of Leeds, UK; and, civil engineers Dr Guillaume Piton and Dr Jean-Marc Tacnet from Université Grenoble Alpes, France.

Reason for submission:

- Return periods of extreme rainfall and flooding events are notoriously difficult to explain to the general public. To circumvent this difficulty, the Wetropolis flood demonstrator was developed by Bokhove and Dutch designer Wout Zweers in response to requests ‒ made by the Environment Agency (EA), Pennine Prospects and JBA Trust ‒ to visualize return periods in a live demonstration [ToR#4, ToR#7].
- The reason for making this submission is to allow the science underlying flood mitigation to become better understood by (international) citizens and the people involved in policy making [ToR#4].
- Moreover, stakeholder involvement at several implementation phases of flood-mitigation plans is becoming increasingly common, but the technical complexity of some strategies, often involving multiple and disparate measures, hampers enlightened and, more importantly, quantifiable, decision-making [ToR#4, ToR#5].

- There is therefore a need for educational tools and sanity checks, such as the one presented here, that facilitate understanding and communication of the efficacy of complex flood-mitigation strategies, additionally because “these [normative] debates are [often] not held in an open and inclusive way, incorporating the views of all stakeholders” (q.v. the introduction in reference [2] below) [ToR#4, ToR#5].
- Finally, the tool has recently been applied in France and Slovenia, where it has been wellreceived by the stakeholders involved [ToR#4, ToR#5].

THE NEW PROTOCOL

### 1. Contextualisation of flood data

### 1.1. Introduction:

The Wetropolis Flood Demonstrator is based on a mathematically and numerically informed model design and has subsequently been built as a transportable physical model [1]. It has been showcased at numerous workshops and exhibitions to approximately 1000 people in 2016-2020. Though initially designed for public outreach, Wetropolis drew the attention of UK flood professionals and academics. By demonstrating what a return period is, Wetropolis pertains to [ToR#4, ToR#7]. It subsequently triggered the development of a new quantitative tool, which has been deployed in analyses of flood-prevention in France and Slovenia, to date, for bridging science and engineering with environmental policy [ToR#4, ToR#5].

This new tool for communicating the integrated magnitude and cost-effectiveness of flood-mitigation schemes has been developed by an international team of researchers comprising UK applied mathematicians and French civil engineers. The new tool deliberately eschews equations and scientific jargon and instead uses a graphical display that shows, as a hypothetical square lake 2 metres deep, the amount of water that needs to be contained in a river valley to stop a river from flooding. The graphic is overlaid with the various options necessary to hold back or to capture the floodwaters, and, more crucially for the purposes of strategic quantification, how much each option will cost. The tool is designed to help both the public and policymakers grasp the headline options and trade-offs inherent in flood-mitigation schemes, and it has already led to better decision-making regarding flood defences in France and Slovenia, particularly where a number of alternatives are being considered. The work grew from a challenge posed by a representative of the Environment Agency (EA) in the UK, who asserted that mathematicians generally explain things in terms of specialist equations and, instead, wanted something that was more accessible: a way of communicating complex ideas clearly and simply, in order to allow the science underlying flood mitigation to be understandable to both citizens and the people involved in policy making alike, thereby addressing [ToR#4, ToR#5].

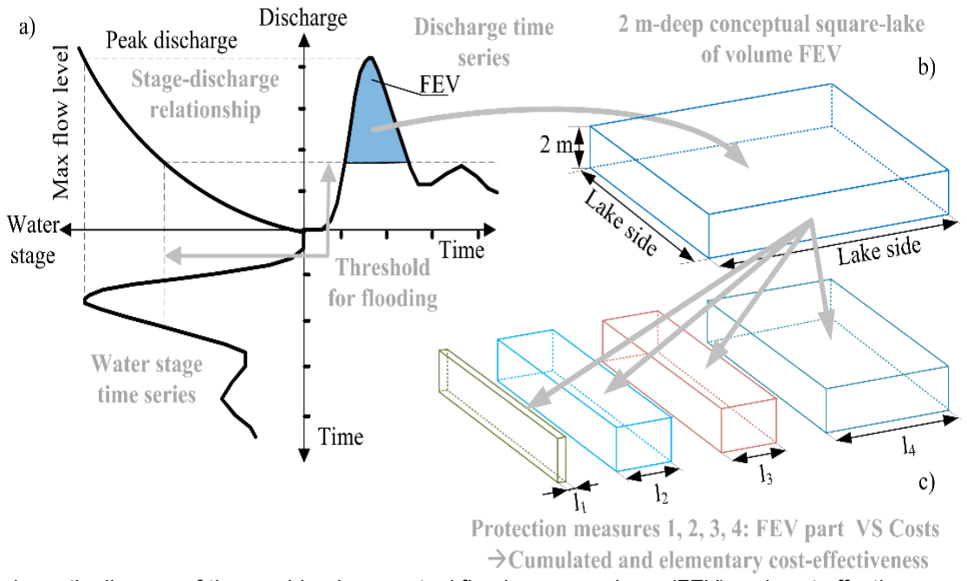
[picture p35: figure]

Fig. 1: Schematic diagram of the combined conceptual flood-excess volume (FEV) and cost-effectiveness approach. (a) Three-panel graph highlighting FEV: (bottom-left) view of river-level time series around a flood event; (top-left) stage-discharge relationship arising from (top-right) discharge data, in which FEV is the blue-coloured “area” between the discharge curve, displayed vertically as function of time horizontally, and a chosen threshold discharge over the duration of the floods, involving in-situ temporal river levels as function of time. (b) FEV square-lake representation as a 2-metre-deep square lake, with side-length “Lake side” being the square root of half the FEV (i.e. FEV divided by 2 metres), to facilitate visualisation of FEV “size”. (c) FEV-effectiveness assessment computed for each measure, here four, as an equivalent FEV fraction, represented as side lengths l1, l2, l3 and l4 of the square lake.

1.2 Background: The research team revisited a concept at the heart of flood analysis: known as “flood-excess volume” (FEV), it is the amount of water in a river system that cannot be contained by existing flood defences. Expressed alternatively, FEV is the amount of water that caused the flooding, expressed as so many thousands or millions of cubic metres of water. Consequently, when this FEV is nullified by one or a variety of flood-mitigation measures, there will be no flood damage in a future flood of similar FEV and/or river levels. However, for most people, including the team of researchers, expressions involving thousands or millions of cubic metres elude meaningful interpretation and/or visualisation. So, instead, FEV is re-expressed in terms of a square lake with a (human-scale) depth of 2 metres. The approach is described in the team’s two recent peer-reviewed international publications [2,3], both of which have been deliberately written in a pedagogical style aimed at a general-yet-interested audience. Fig. 1 depicts a schematic diagram of the methodology underlying the philosophy used in [2,3], thereby highlighting that FEV pertains to [ToR#4] via the education of citizens, cf. the use of hydrographs in Slow-the-Flow.

1.3 Exemplification: To illustrate the idea, data have been analysed from the floods on Boxing Day 2015, when the River Aire burst its banks in Leeds and caused extensive damage to homes and businesses; damage estimated at around half a billion pounds. Around 9.34 million cubic metres of water flooded from the River Aire on Boxing Day 2015 into the Kirkstall/Armley area of Leeds. Such a volume of flood water translates into a hypothetical square lake of depth 2 metres, with sides of length 2161 metres. By comparison, the upper River Aire is about 50 miles long, with a valley width that varies along its path roughly between 200 and 600 metres. To have prevented the Boxing Day 2015 flood, one would have had to somewhere deal with that volume of water. It is not inconceivable that, along the course of the river, additional water storage could have been accommodated, either by increasing the size of flood plains or by removing obstructions in the river, widening the river channel in places (also called givingroom-to-the-river or GRR) or by building higher flood walls. More likely, one would have needed to combine some or all of these measures. Visualising flood mitigation in this new way makes it easier for people to understand not only the interventions that are possible – i.e. their size and the impact they are likely to have – but also the costs associated with each such constituent flood-mitigation measure. This example relates to [ToR#4, ToR#5] because it not only advises the public on flood-mitigation measures but also, in particular, on Natural Flood Management (NFM).

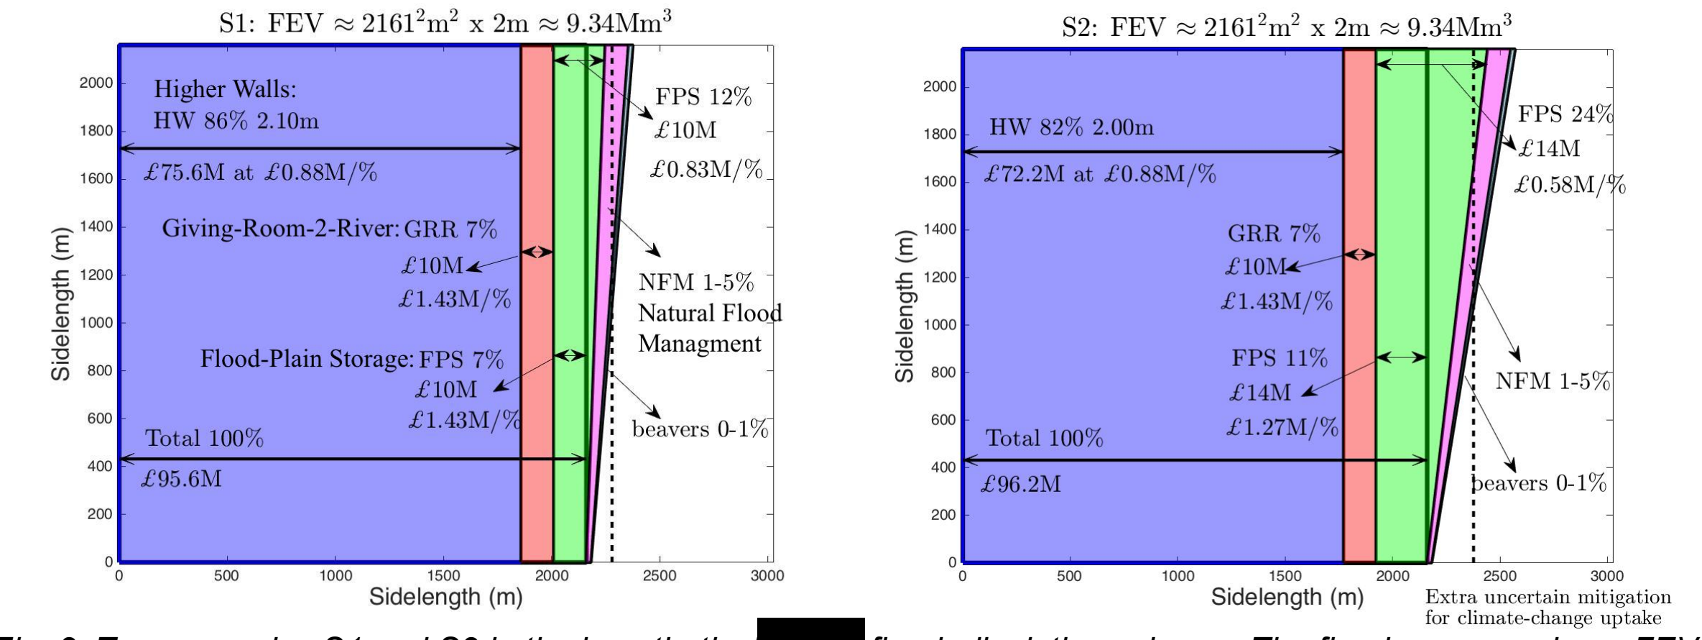
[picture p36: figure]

Fig. 2: Two scenarios S1 and S2 in the hypothetical Leeds flood-alleviation scheme. The flood-excess volume FEV of 9.34 million cubic metres of the Leeds’ Boxing Day 2015 floods (the FEV that caused the flood damage) is represented as a square lake (viewed from above) of depth 2 metres with sides of length 2161 metres (about 1.25 miles). Each coloured segment represents the portion of the hypothetical square lake absorbed by a specific mitigation measure. Cost and cost per percentage covered per mitigation measure (i.e. by each segment) are displayed (above and below) the double-sided arrow pertaining to that segment, as well as the total or overall costs of that scenario. Additional-yet-uncertain mitigation is offered in part by flood-plain storage (FPS, green), or via Natural Flood Management (NFM, pink) and 85 beaver colonies (the small silver sliver). For a large flood such as that of Boxing Day 2015, the contribution of NFM and 85 beaver colonies is small-to-minute, as well as uncertain, leading to the two thin pink and silver slivers, which are small in area relative to the areas of other measures such as higher walls (HW, dark purple) and river-bed widening (GRR, red). Scenario S1 concerns a case with flood-plain storage in Calverley and scenario S2 one with larger flood-plain storage in Rodley, both areas being within 7 miles of Leeds. (Images adapted from [2], in which also three other scenarios are introduced and compared.)

### 2. Scoping and planning

2.1 Cost-effectiveness visualisation: The researchers have used their novel graphical approach to analyse and to communicate a hypothetical scheme for increasing the flood defences in the Kirkstall/Armley area of Leeds, upstream of Leeds’ City (railway) Station, to cope with not only a major flood that would be expected once in 100 years but also a once-in-200-year flood. They looked at several mitigation scenarios, their costs and their impact on river dynamics, a sub-topic of the scientific discipline of “fluid dynamics”, in which the University of Leeds is a world leader. The accompanying graphics in Fig. 2 show two such hypothetical scenarios. With colour-coded overlays, it shows how higher flood-defence walls (denoted by HW), more flood-plain storage (denoted by FPS) and riverwidening (denoted by GRR) could provide the additional drainage necessary to avert a repeat of the scale of flooding seen in 2015. Another graphical analysis in Fig. 3, of the River Calder Boxing Day 2015 flood in Mytholmroyd, highlights, in terms of sloping lines, bounds on the inherent uncertainty in flood-mitigation measures: the use of water reservoirs in the upper catchment to hold rain water by drawing down reservoir levels is seen to be potentially very effective relative to the smaller contributions of tree planting and leaky dams, even though tree planting and the number of leaky dams have been upscaled to a deliberately exaggerated level that greatly exceeds that in existing plans. Several such analyses, investigated in [2,3] and presented by the team at various national and international meetings, reveal the limited impact of Natural Flood Management (denoted by NFM). That is, in stark contrast to what many people in the UK are led to believe, the planting of trees or the introduction of “realistically
numerous” beaver colonies to build dams can at best have limited impact on the mitigation of bigger floods. In summary, the visualisation approach directly pertains to [ToR#4] through both its involvement of the public and the support it offers to decision-making.

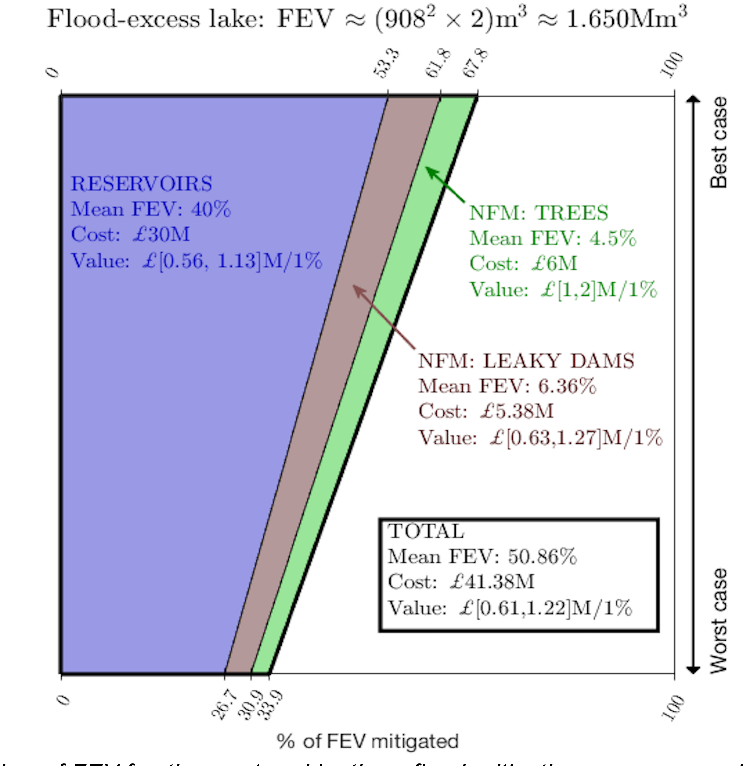
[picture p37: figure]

Fig. 3: Graphical overview of FEV fraction captured by three flood-mitigation measures and associated costs for the River Calder at Mytholmroyd. The FEV here is 1.65 million cubic metres and is represented as a 2-metre-deep square lake of side-length 908m. Overall flood-mitigation ranges from 33.90% to 67.81% at a cost of £41.38 million. The mean contribution of each of the constituent flood-mitigation measures is represented by corresponding quadrilateral areas, indicated by “reservoirs” (purple), “NFM: trees” (brown) and “NFM: leaky dams” (green); together, these partition the overall square-lake area with the same FEV capacity requiring mitigation. Sloping lines reflect the sliding scale between quoted ranges accruing from storage-capacity uncertainty. The remaining (white) area should be covered by other measures, such as in-situ higher walls or river-bed widening (i.e. GRR) in Mytholmroyd. (Image reproduced from [3].)

2.2 Protocol-application credentials: The newly developed tool can be and has already been used in two ways. Given in-situ flood data, it can provide a quick a priori investigation to explore and to propose various flood-mitigation scenarios: in this vein, a non-governmental organisation in Slovenia [4] has used the tool to explore the effectiveness of Nature Based Solutions in flood mitigation. Alternatively, it can be used a posteriori as an executive summary of complicated, costly and extensive computer simulations undertaken by engineers. In the latter case, the new tool offers a relatively cheap and easy-to-implement protocol and sanity check of such technical calculations for not only decision-makers and citizens but also for the technical experts involved. The French civil engineers in the team that designed the tool have used it to communicate complicated hydrodynamic simulations for the River Brague in South-East France, following devastating floods there in 2015 and, more recently, in 2019.

Additionally, recent 2019-2020 winter floods in both the UK and Indonesia have been and continue to be analysed in undergraduate projects that have deployed our approach. This analysis has already highlighted that essential river-discharge data are sometimes missing from data currently gathered by the EA, and that this lack of data partly obstructs the construction of flood-mitigation plans requiring FEV. That is, through the use of our protocol, an important novel conclusion – that current data gathering may be suboptimal – has been revealed. In summary, our protocol directly pertains to [ToR#4], involving the public and support decision-making.

2.3 Bespoke flood-evacuation warning/plan: During the 2015 Boxing Day floods in Leeds, an ad hoc flood evacuation of local business Xfit The Forge (XTF) was triggered by an author (OB) of [2]. This was based on the levels and their rate of increase (as recorded on the nearby Armley river gauge) of the River Aire during the flood, as well as local knowledge of critical flood levels for XTF, the latter being acquired during observations of a minor-flood peak in mid December 2015. Over £5000 of gym equipment was saved and XTF could consequently re-open quickly, as one of the first on the Kirkstall business estate. This ad hoc plan was subsequently formalized by OB in [5], and (re-)used during Storm Ciara in February 2020 (after OB had issued a warning on the day) by XTF for its evacuation of gym equipment; the plan had moreover been shared by the owner of XTF with nearby businesses. While XTF escaped flooding with only 10cm to spare, nearby premises were indeed flooded by Storm Ciara. The essence of the bespoke plan is that it uses local (photographic) evidence to augment, with timings regarding evacuation, warnings provided by the EA. This hands-on experience triggered work that led to papers [2,3] and provided first-hand evidence factually used in [2]. Although the use of this particular extended flood-evacuation plan from February 2020 pertains to [ToR#7], it is important to stress that is not only readily adapted to other locations, but also can be automated using modern Data Science methodology, thereby specifically addressing quantification of the “level of investment … required” in [ToR#3] and being a proactive contributor to the “communities most effectively … involved …” in [ToR#4].

2.4 Contribution to future UK policy: Finally, though the UK Government will over the six years to 2021 have spent £2.6 billion [6] on flood schemes in England, further investment is expected. Specifically, it aims to increase such spending in the manner recently announced by the UK Environment Secretary [7]. Thus the new approach could well prove useful in its intended role of offering a protocol for comparing and choosing between flood-mitigation scenarios in a quantifiable, evidence-based and visual manner, thereby offering a better chance of the available options and costs being understood and accepted by a wide audience including the general public, stakeholders and planners. In summary, our education demonstrator Wetropolis, our decision-making tool and our extended flood-evacuation plan pertain to [ToR#3, ToR#4, ToR#5, ToR#7].

References
[1] Wetropolis Flood Demonstrator, GitHub design site: https://github.com/obokhove/wetropolis20162020
[2] Bokhove, O., Kelmanson, M.A., Kent. T., Piton, G. and Tacnet, J.-M., A cost-effectiveness protocol for flood-mitigation plans based on Leeds' Boxing Day 2015 floods, Water 12(3), 652-682, 2020. https://www.mdpi.com/2073-4441/12/3/652
[3] Bokhove, O., Kelmanson, M.A., Kent. T., Piton, G. and Tacnet, J.-M., Communicating (nature-based) flood-mitigation schemes using flood-excess volume, River Res. Appl. 35(9), 1402-1414, 2019. https://onlinelibrary.wiley.com/doi/full/10.1002/rra.3507
[4] Slovenian Instituto Revivo, http://www.ozivimo.si/en/
[5] 2015 Flood-evacuation plan for Xfit The Forge: https://github.com/obokhove/wetropolis20162020/blob/master/BokhoveXfitPlan.pdf Facebook-Messenger correspondence, comments/photographs, during Storm Ciara: https://bardvantwenthe.wordpress.com/2020/02/29/kirkstall-flood-evacuation-during-storm-ciara/
[6] https://www.gov.uk/government/news/government-pledges-62m-flood-funding-for-communities-inengland
[7] Quote by George Eustice, UK Environment Secretary on page 3 of transcript: http://news.bbc.co.uk/1/shared/bsp/hi/pdfs/23022001.pdf of Andrew Marr Show, BBC1, 23/02/2020.

2022: it was
~20k

Part 2: Discussion on “A new tool for communicating cost-effectiveness of flood-mitigation schemes”

Background

The FEV cost-effectiveness tool revealed inconsistencies in LFAS2 [1] communicated to LCC in 2017-18; thus revealed, they must later have been removed by LCC in the revision of LFAS2 in order to ensure that Defra and the Executive Board would not subsequently be confronted with them. It is additionally noted that targeted LCC and EA recipients of early (pre-publication) drafts of journal papers [2,3] and the tool/protocol [4] elicited no substantive feedback throughout 2017-20. Therefore, the following discussion between the authors of [1] ([C]omments in black) and [2,3,4] ([R]responses in blue) provides the first substantive and interesting exchange on the matter.

Discussion

- [C1] In summary, I would probably kindly discourage the use of FEV as I think it misses the point a little. However, the plots shown are useful in terms of build up of measures and how they build in a modular way to create a solution – I just think this needs to be in terms of flow reduction towards a threshold of flooding (in flow) rather than volume/FEV. Then I think this would be a useful way of communicating what each measure does in terms of necessary flood risk prevention v how much it will cost.

[R1] Since the (cross-sectional) “flow” mentioned in [C1] is expressed in m³
/s, temporal
integration above a flow or water-level threshold (related via a rating curve) gives one the FEV. That is, FEV is the temporal integration of a dynamic quantity, so FEV is hereafter referred to as dFEV to highlight unequivocally its dynamic origin. Note too that all flood-mitigation measures used in the (NB virtual) square-lake representations in [2,3], for various international scenarios and rivers, are similarly based on temporal integrations of dynamic flow.
- [C2] FEV (as you’ve presented) is a very useful tool for describing the size of a flood management problems, specifically for a particular event.

[R2] In the road-map in [2], specifically advocated is the use of ensemble predictions leading to ensemble dFEVs and ensemble flood-mitigation scenarios, i.e. concerning an ensemble of flood events. However, in order to introduce/exemplify the methodology, focus was deliberately placed on particular worst-case events.

- [C3] However, there is a real risk here that using this as an example means that interested parties focus on storage based solutions, rather than the whole suite of potential flood management measures that we have at our disposal and their physical impact – for example improving conveyance (which reduces the FEV for a specific event, but doesn’t store it, or NFM infiltration improvements, raised walls etc. all of which have a similar impact, but not by storing water, just by reducing the volume that exceeds the defence or channel capacity and therefore reducing the FEV.

[R3] The “focus on storage-based solutions” mentioned in [C3] is manifestly not advocated in [2,3], in which the square-lake graphs for various scenarios and rivers (with different colours for each flood-mitigation measure) clearly show that, in all but one case, a handful of flood-mitigation measures (some of which are mentioned in [C3]) are considered. These include higher walls, giving room to the river (GRR), dynamic flood-plain storage (using controllable weirs), NFM (including e.g. leaky dams, trees, beavers), dynamic draw-down of reservoirs. That is, explicit and deliberate consideration is given to the "whole suite of potential flood management measures" mentioned in [C3] , including GRR for "improving conveyance" (see https://www.preventionweb.net/publications/view/59399). In one case higher walls in isolation are considered, but only because this ties in with the explicit highlighting in [2] of the observation that LFAS2 is based on ~85% dFEV reduction via higher walls augmented by ~15% dFEV reduction via GRR and flood-plain storage, and ~0%-5% (extra) dFEV reduction via NFM; the last figure of ~0%-5% was stated in a public meeting at Kirkstall in early 2019.

- [C4] In the text it does refer to these impacts on a storage basis, which is wrong and quite confusing to the lay person – or misleading when factoring in conveyance.

[R4] Referring to [R3], the factoring in of conveyance is indeed considered and so the classification in [C4] of the approach as "wrong and quite confusing" is not merited since it advocates not only GRR but also a variety of flood-mitigation measures, only one of which is (dynamic) flood-plain storage. Papers [2,3] moreover highlight approaches in which none of the mitigation measures itself exceeds ~50% of the total. Also, in [2,3], dFEV has been repeatedly qualified as the effective volume in order to contrast it with a static volume (which it is not). Moreover, stakeholders in both France and Slovenia particularly appreciated that expressing each mitigation measure as a (dynamic) volume conveys a sense of size of that measure, also relatively to another, which (sense of size) hitherto was generally missing in communication with stakeholders, decision-makers and the public.

- [C5] FEV is concerning also, as it ties its case to volume.

[R5] As stated in [R1], the term dFEV now supercedes the hitherto-used “effective volume”, noting that both terms emphasise its foundation on integrated flow rather than on storage/static volume per se.

- [C6] However, we know that for a given rarity event the volume can change significantly depending on duration, storm coverage and rainfall intensity.

[R6] As stated in [R2], in [2,3] the use is advocated of ensemble forecasting based on a variety of events. However, by mitigating against a rare event involving a combination of a peak water level with a peak flood volume (a temporally integrated discharge/flow), one automatically
also mitigates against an event with a (similar) high water level yet shorter duration. In fact, a mixture of GRR, floodwater storage, use of reservoirs and NFM optimally mitigates against both types of events without the need to excessively increase wall heights in cities.
- [C7] This means that for the same target SoP using FEV as a descriptor would change depending on the hydrological nature of the scenario you were describing, which becomes quite complicated and probably would undo some of the benefit of a simple message.

[R7] In [2], the use is advocated of both dFEV and water levels to calculate return periods leading to (slightly) different classifications; in combination with the use of ensemble forecasting this does cover a range of flooding events and scenarios. In the case of ensemble forecasting, one can also represent the mean results as in [2] to keep it simple but, additionally, one can convey the uncertainty arising from such ensemble predictions via the slanted lines already included in [2, Fig. 10]. Representing uncertainty in a clear manner is something worthwhile for further investigation.

The FEV cost-effectiveness tool can moreover be used either for a priori exploration of flood-mitigation scenarios when time and/or computational resources are lacking (often based on data of one flood event or a few flood events), or for an a posteriori executive summary of extensive computer predictions for flood mitigation (possibly including uncertainty quantification using ensemble predictions). Within these contexts, in 2019 the dFEV approach explicitly underpinned not only an a priori cost-effectiveness analysis of NFM by a Slovenian NGO regarding floods affecting the city of Ljublana, but also an a posteriori cost-effectiveness analysis by French civil engineers, thereby supporting communication and decision-making for the municipality of Sophia Antipolis in France.

Hence the dFEV approach offers a hybrid tool somewhere between technical hydraulic calculations and decision-aiding, which often emerge as the challenging parts of the whole design process.

References

[1] Dennis, R., Phase 2 Leeds (River Aire) Flood Alleviation Scheme (LFAS2), Report to LCC Executive Board, December 2017. See “Flood alleviation cover report 041217” at host page https://democracy.leeds.gov.uk/ieDecisionDetails.aspx?ID=45047
[2] Bokhove, O., Kelmanson, M.A., Kent. T., Piton, G. and Tacnet, J.-M., A cost-effectiveness protocol for flood mitigation plans based on Leeds' Boxing Day 2015 floods, Water 12(3), 652-682, 2020. https://www.mdpi.com/2073-4441/12/3/652
[3] Bokhove, O., Kelmanson, M.A., Kent. T., Piton, G. and Tacnet, J.-M., Communicating (nature-based) flood mitigation schemes using flood-excess volume, River Res. Appl. 35(9), 1402-1414, 2019. https://onlinelibrary.wiley.com/doi/full/10.1002/rra.3507
[4] Bokhove, O., Kelmanson, M.A., Kent, T. A new tool for communicating cost-effectiveness of flood-mitigation schemes, written evidence, document no. FLO0074 (https://committees.parliament.uk/writtenevidence/9641/pdf/) to Defra Flooding Enquiry (https://committees.parliament.uk/work/107/flooding), September 2020.

Onno Bokhove and Mark Kelmanson October 2nd 2020.

Part 3: Schematic overview of the flood-policy method.

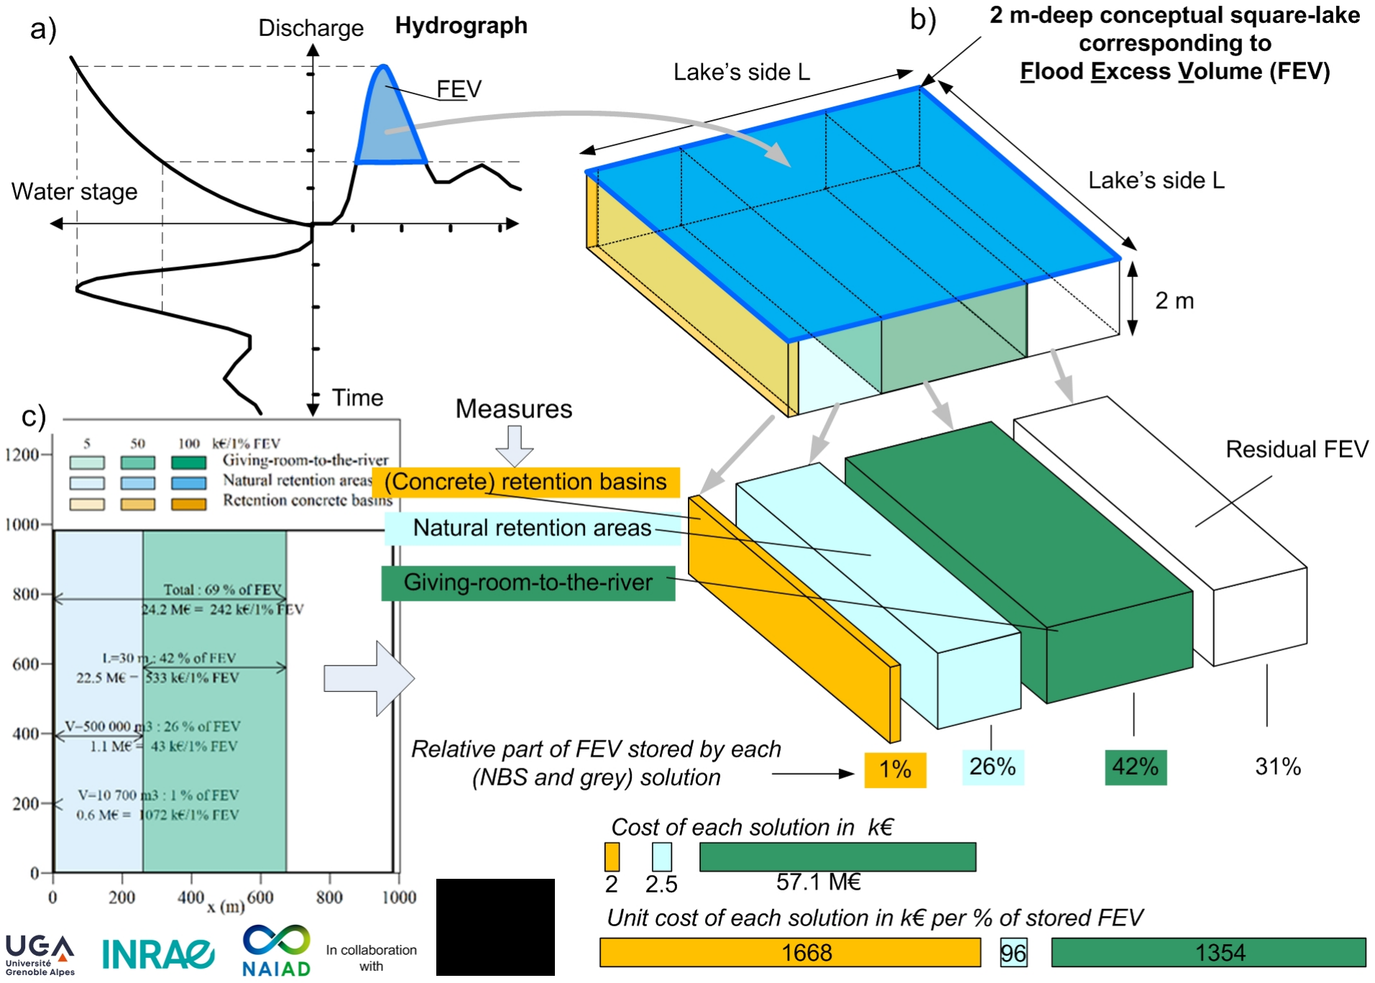
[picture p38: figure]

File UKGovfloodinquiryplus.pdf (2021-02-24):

### A new tool for communicating cost-effectiveness of flood-mitigation schemes: DEFRA inquiry submission and schematic

Onno Bokhove¹

, Mark Kelmanson¹

, Tom Kent¹

, Guillaume Piton² and Jean-Marc Tacnet² 1 School of Mathematics and Leeds Institute for Fluid Dynamics (LIFD), University of Leeds, Leeds LS2 9JT, W. Yorks., UK 2 Univ. Grenoble Alpes, INRAE, UR ETGR, Centre de Grenoble, F-38402, Saint-Martin-d’Hères, France

October 29th 2020

Resumé This document is an amalgamative overview of materials emerging from both work on a new flood-mitigation protocol conducted by the authors since 2017.

- Part 1 of the following comprises the verbatim text of a September 2020 submission by the authors to an ongoing DEFRA committee inquiry into flooding.
- Part 2 is a graphical overview of the authors’ protocol that augments Figure 1 of Part 1 in both a quantified and visually striking way.

Part 1 : Environment, Food and Rural Affairs Committee inquiry into flooding

Submission: A new tool for communicating cost-effectiveness of flood-mitigation schemes

Summary:

- The “Wetropolis” flood-outreach demonstrator has been developed at Leeds to enable live visualisation of so-called return periods of extreme rainfall and flooding events to the general public.
- A team of Leeds mathematicians and French civil engineers has developed a novel and innovative way of visualising and analysing complex flood-protection schemes.
- This protocol, or tool, has been designed with the express intention of empowering decision-makers and flood action groups, as well as the general public, to make quantified judgements on the cost-effectiveness of flood-mitigation plans in order to facilitate enhanced evidence-based decision-making. The tool enables rapid a priori, as well as thorough a posteriori, comparisons to be made of various flood-mitigation options and scenarios.
- To date, the tool has highlighted that, in contrast to media promulgation, the effectiveness of Natural Flood Management (NFM) in the mitigation of medium- to large-size floods is small, if not minute. For example, at least 8500 beaver colonies — an unrealistic and unattainable upscaling — would be required to mitigate the notorious Boxing Day 2015 floods in Leeds.
- The tool is, however, objective, and so could equally highlight that for certain floods – i.e. sufficiently small and localized, with a “flood-excess volume” (see section 1.2 below for definition) of less than ~10,000 cubic metres, one beaver colony could potentially mitigate ~20% of the damage, with the remaining ~80% needing to be absorbed by other flood-mitigation measures.
- Hence, referring to the ToR, the new tool demonstrably addresses how “communities can be involved most effectively” [ToR#4] in flood mitigation, how “increasing focus on natural flood management measures” [ToR#5] has to be put in an evidence-based context of being predominantly relevant for the mitigation of small-scale floods, and how “lessons can be learned from the recent winter floods” [ToR#7]. We subsequently refer in bold, with accompanying reasons, to where [ToR#3, ToR#4, ToR#5, ToR#7] are relevant in the main text.

Researchers involved:

- The work is a collaboration between applied mathematicians Professor Onno Bokhove, Professor Mark Kelmanson and Dr Tom Kent from the School of Mathematics at the University of Leeds, UK; and, civil engineers Dr Guillaume Piton and Dr Jean-Marc Tacnet from Université Grenoble Alpes, France.

Reason for submission:

- Return periods of extreme rainfall and flooding events are notoriously difficult to explain to the general public. To circumvent this difficulty, the Wetropolis flood demonstrator was developed by Bokhove and Dutch designer Wout Zweers in response to requests ‒ made by the Environment Agency (EA), Pennine Prospects and JBA Trust ‒ to visualize return periods in a live demonstration [ToR#4, ToR#7].
- The reason for making this submission is to allow the science underlying flood mitigation to become better understood by (international) citizens and the people involved in policy making [ToR#4].
- Moreover, stakeholder involvement at several implementation phases of flood-mitigation plans is becoming increasingly common, but the technical complexity of some strategies, often involving multiple and disparate measures, hampers enlightened and, more importantly, quantifiable, decision-making [ToR#4, ToR#5].

- There is therefore a need for educational tools and sanity checks, such as the one presented here, that facilitate understanding and communication of the efficacy of complex flood-mitigation strategies, additionally because “these [normative] debates are [often] not held in an open and inclusive way, incorporating the views of all stakeholders” (q.v. the introduction in reference [2] below) [ToR#4, ToR#5].
- Finally, the tool has recently been applied in France and Slovenia, where it has been wellreceived by the stakeholders involved [ToR#4, ToR#5].

THE NEW PROTOCOL

### 1. Contextualisation of flood data

### 1.1. Introduction:

The Wetropolis Flood Demonstrator is based on a mathematically and numerically informed model design and has subsequently been built as a transportable physical model [1]. It has been showcased at numerous workshops and exhibitions to approximately 1000 people in 2016-2020. Though initially designed for public outreach, Wetropolis drew the attention of UK flood professionals and academics. By demonstrating what a return period is, Wetropolis pertains to [ToR#4, ToR#7]. It subsequently triggered the development of a new quantitative tool, which has been deployed in analyses of flood-prevention in France and Slovenia, to date, for bridging science and engineering with environmental policy [ToR#4, ToR#5].

This new tool for communicating the integrated magnitude and cost-effectiveness of flood-mitigation schemes has been developed by an international team of researchers comprising UK applied mathematicians and French civil engineers. The new tool deliberately eschews equations and scientific jargon and instead uses a graphical display that shows, as a hypothetical square lake 2 metres deep, the amount of water that needs to be contained in a river valley to stop a river from flooding. The graphic is overlaid with the various options necessary to hold back or to capture the floodwaters, and, more crucially for the purposes of strategic quantification, how much each option will cost. The tool is designed to help both the public and policymakers grasp the headline options and trade-offs inherent in flood-mitigation schemes, and it has already led to better decision-making regarding flood defences in France and Slovenia, particularly where a number of alternatives are being considered. The work grew from a challenge posed by a representative of the Environment Agency (EA) in the UK, who asserted that mathematicians generally explain things in terms of specialist equations and, instead, wanted something that was more accessible: a way of communicating complex ideas clearly and simply, in order to allow the science underlying flood mitigation to be understandable to both citizens and the people involved in policy making alike, thereby addressing [ToR#4, ToR#5].


Fig. 1: Schematic diagram of the combined conceptual flood-excess volume (FEV) and cost-effectiveness approach. (a) Three-panel graph highlighting FEV: (bottom-left) view of river-level time series around a flood event; (top-left) stage-discharge relationship arising from (top-right) discharge data, in which FEV is the blue-coloured “area” between the discharge curve, displayed vertically as function of time horizontally, and a chosen threshold discharge over the duration of the floods, involving in-situ temporal river levels as function of time. (b) FEV square-lake representation as a 2-metre-deep square lake, with side-length “Lake side” being the square root of half the FEV (i.e. FEV divided by 2 metres), to facilitate visualisation of FEV “size”. (c) FEV-effectiveness assessment computed for each measure, here four, as an equivalent FEV fraction, represented as side lengths l1, l2, l3 and l4 of the square lake.

1.2 Background: The research team revisited a concept at the heart of flood analysis: known as “flood-excess volume” (FEV), it is the amount of water in a river system that cannot be contained by existing flood defences. Expressed alternatively, FEV is the amount of water that caused the flooding, expressed as so many thousands or millions of cubic metres of water. Consequently, when this FEV is nullified by one or a variety of flood-mitigation measures, there will be no flood damage in a future flood of similar FEV and/or river levels. However, for most people, including the team of researchers, expressions involving thousands or millions of cubic metres elude meaningful interpretation and/or visualisation. So, instead, FEV is re-expressed in terms of a square lake with a (human-scale) depth of 2 metres. The approach is described in the team’s two recent peer-reviewed international publications [2,3], both of which have been deliberately written in a pedagogical style aimed at a general-yet-interested audience. Fig. 1 depicts a schematic diagram of the methodology underlying the philosophy used in [2,3], thereby highlighting that FEV pertains to [ToR#4] via the education of citizens, cf. the use of hydrographs in Slow-the-Flow.

1.3 Exemplification: To illustrate the idea, data have been analysed from the floods on Boxing Day 2015, when the River Aire burst its banks in Leeds and caused extensive damage to homes and businesses; damage estimated at around half a billion pounds. Around 9.34 million cubic metres of water flooded from the River Aire on Boxing Day 2015 into the Kirkstall/Armley area of Leeds. Such a volume of flood water translates into a hypothetical square lake of depth 2 metres, with sides of length 2161 metres. By comparison, the upper River Aire is about 50 miles long, with a valley width that varies along its path roughly between 200 and 600 metres. To have prevented the Boxing Day 2015 flood, one would have had to somewhere deal with that volume of water. It is not inconceivable that, along the course of the river, additional water storage could have been accommodated, either by increasing the size of flood plains or by removing obstructions in the river, widening the river channel in places (also called givingroom-to-the-river or GRR) or by building higher flood walls. More likely, one would have needed to combine some or all of these measures. Visualising flood mitigation in this new way makes it easier for people to understand not only the interventions that are possible – i.e. their size and the impact they are likely to have – but also the costs associated with each such constituent flood-mitigation measure. This example relates to [ToR#4, ToR#5] because it not only advises the public on flood-mitigation measures but also, in particular, on Natural Flood Management (NFM).


Fig. 2: Two scenarios S1 and S2 in the hypothetical Leeds flood-alleviation scheme. The flood-excess volume FEV of 9.34 million cubic metres of the Leeds’ Boxing Day 2015 floods (the FEV that caused the flood damage) is represented as a square lake (viewed from above) of depth 2 metres with sides of length 2161 metres (about 1.25 miles). Each coloured segment represents the portion of the hypothetical square lake absorbed by a specific mitigation measure. Cost and cost per percentage covered per mitigation measure (i.e. by each segment) are displayed (above and below) the double-sided arrow pertaining to that segment, as well as the total or overall costs of that scenario. Additional-yet-uncertain mitigation is offered in part by flood-plain storage (FPS, green), or via Natural Flood Management (NFM, pink) and 85 beaver colonies (the small silver sliver). For a large flood such as that of Boxing Day 2015, the contribution of NFM and 85 beaver colonies is small-to-minute, as well as uncertain, leading to the two thin pink and silver slivers, which are small in area relative to the areas of other measures such as higher walls (HW, dark purple) and river-bed widening (GRR, red). Scenario S1 concerns a case with flood-plain storage in Calverley and scenario S2 one with larger flood-plain storage in Rodley, both areas being within 7 miles of Leeds. (Images adapted from [2], in which also three other scenarios are introduced and compared.)
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

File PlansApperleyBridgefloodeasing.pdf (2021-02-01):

Draft 01-02-2021 Onno Bokhove, Apperley Bridge, UK; onnobokhove@gmail.com | 1

## Leeds’ plans for flood easing from Apperley Bridge to Calverley

Regarding Leeds’ flood-mitigation plans for Apperley Bridge, Bradford

Remarks on general aspects of the plan are first given, followed by a discussion and questions on its specifics. The main observation to note is that the existing flood-easing plans [1] for Apperley Bridge are difficult to assess in any quantitative sense given that they contain neither alternative scenarios nor discussion of costs and cost-effectiveness thereof, thereby materially degrading the plan’s presumably intended purpose of enhancing evidence-based decision-making, such as that developed and promoted in [2].

General remarks are as follows:
i. The plans in [1] do not protect against floods of a similar size to the Boxing Day 2015 flood, but only against lesser floods with a 1-in-200-years (or less) return period. As such, overtopping of the proposed flood defense walls and flooding would occur for a flood of similar size or larger than the Boxing Day 2015 flood, since that flood was approximately a 1-in-250-years or 1-in-300-years flood.
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

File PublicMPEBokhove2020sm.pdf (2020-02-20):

Flooding: should we be worried?; Onno Bokhove; Who am I?; Introduction; Rain in future?; Extreme precipitation & flooding?; Wetropolis; Predict heavy precipitation & floods?; Mitigate flooding?; Test things?; Worried enough?; should we be more worried?

# Managing river floods in an age of extremes:

## School of Mathematics, University of Leeds, Yorkshire, UK Teamwork: Hicks, Kelmanson, Kent, Piton, Tacnet & Zweers! Churchtown & Wainfleet Flood Action Groups
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

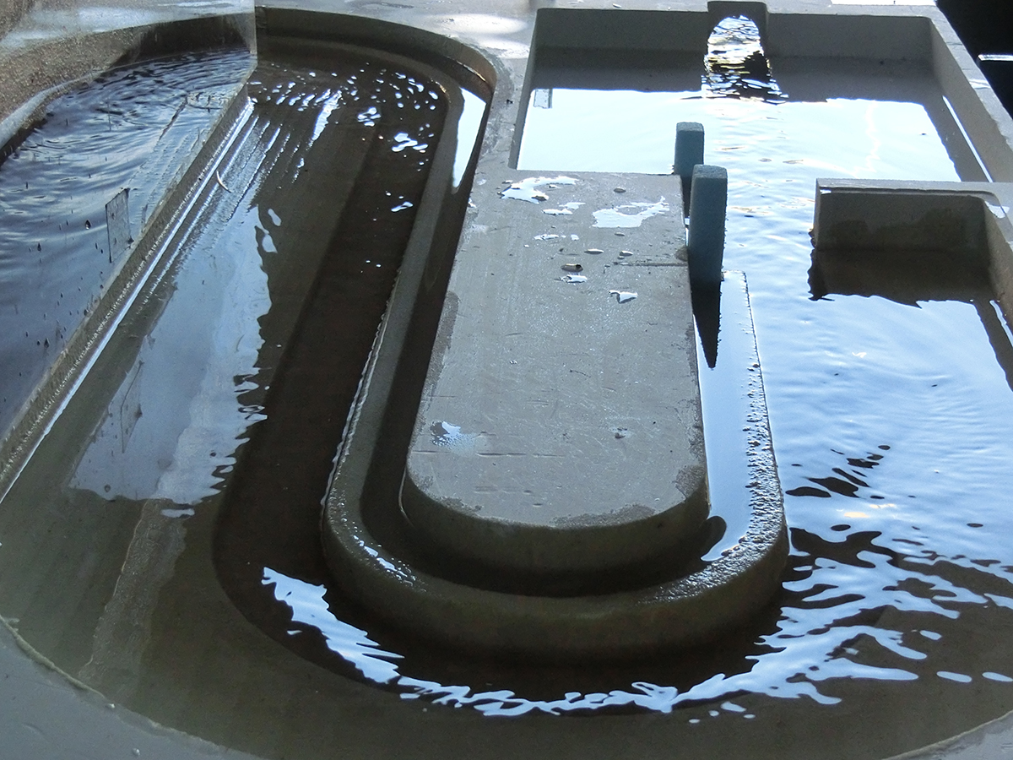
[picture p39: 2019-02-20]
figs/20161708CIMG2146copy.jpg

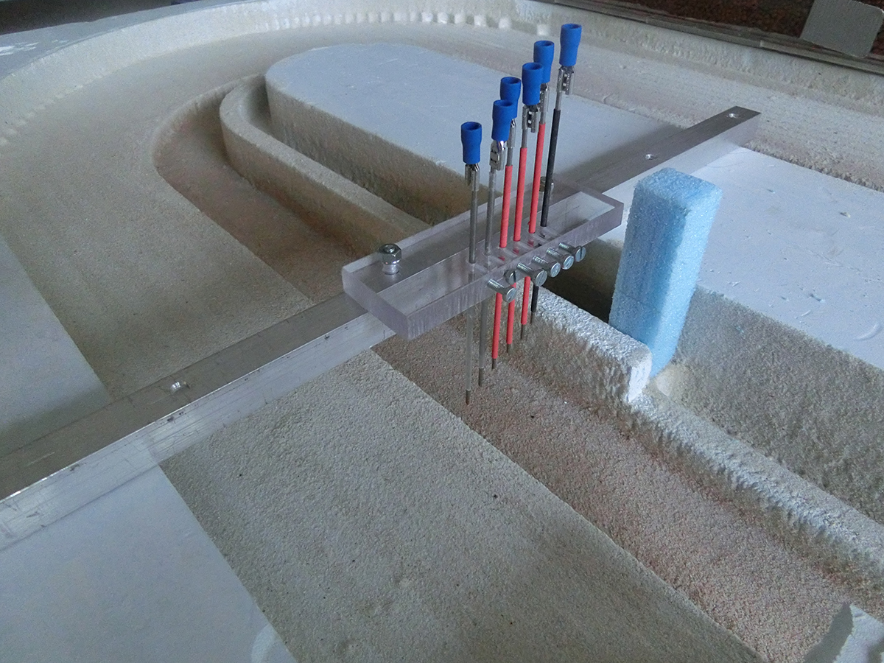
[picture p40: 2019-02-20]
figs/20162208CIMG2212copy.jpg

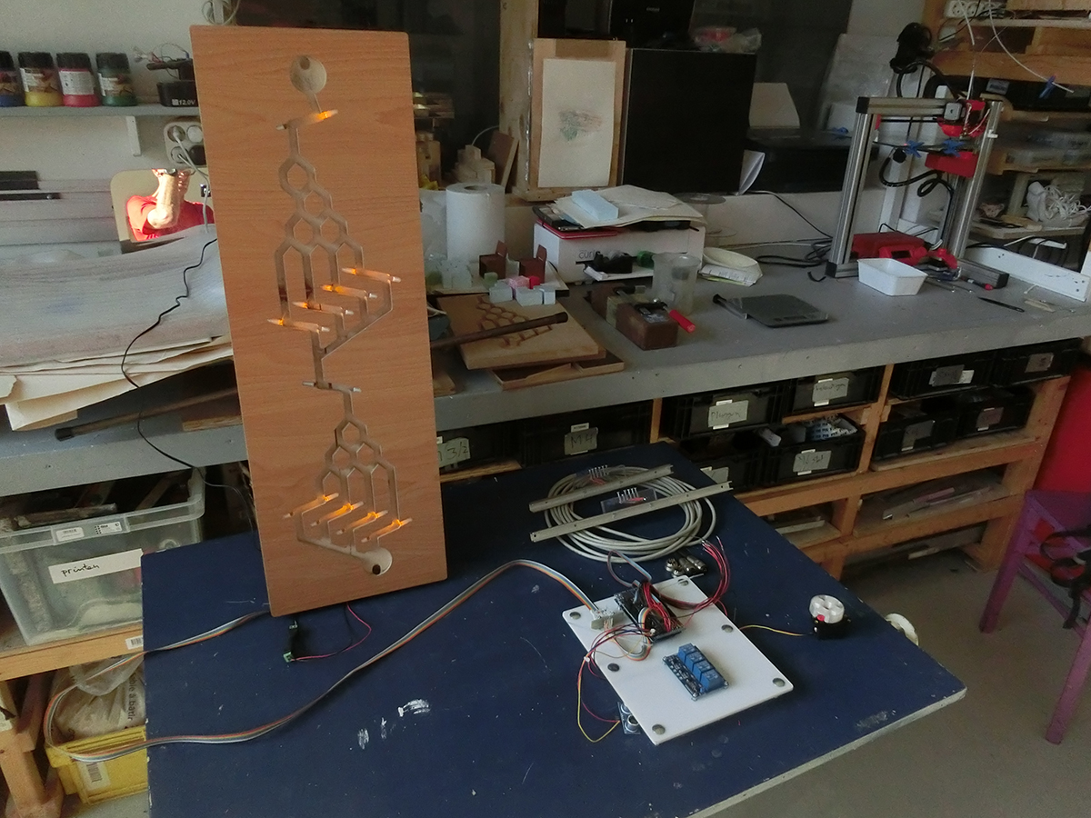
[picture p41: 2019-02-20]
figs/20162608CIMG2276copy.jpg

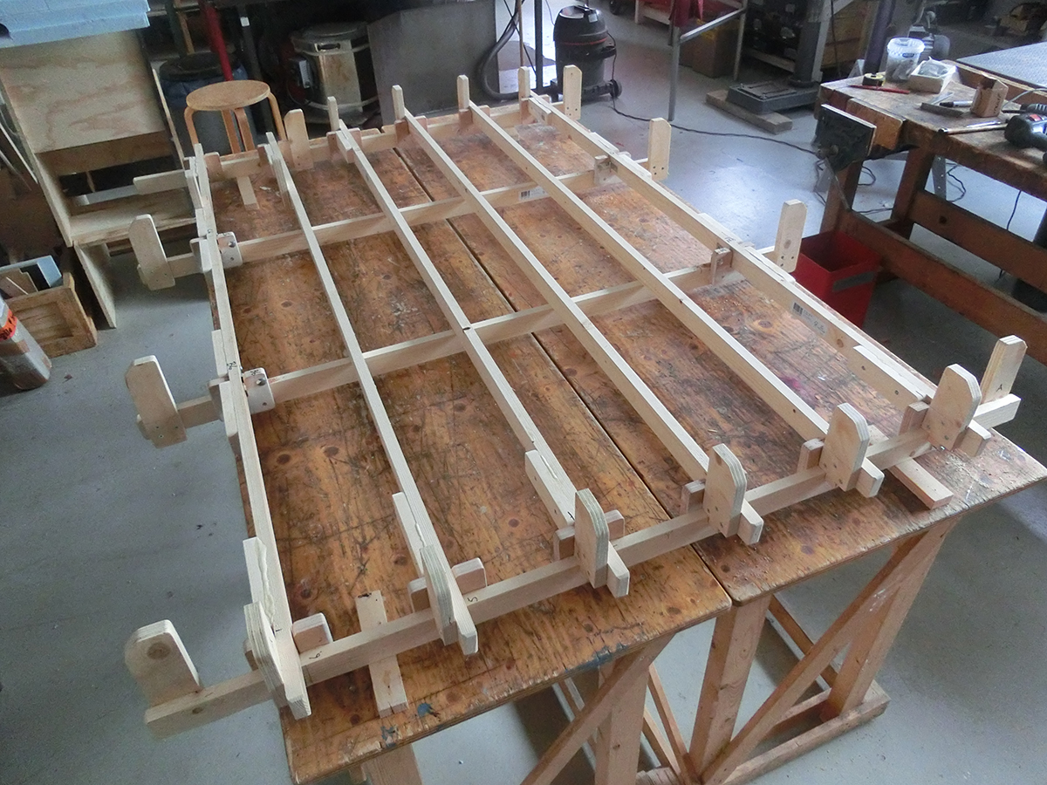
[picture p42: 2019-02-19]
figs/20162107CIMG1741copy.jpg

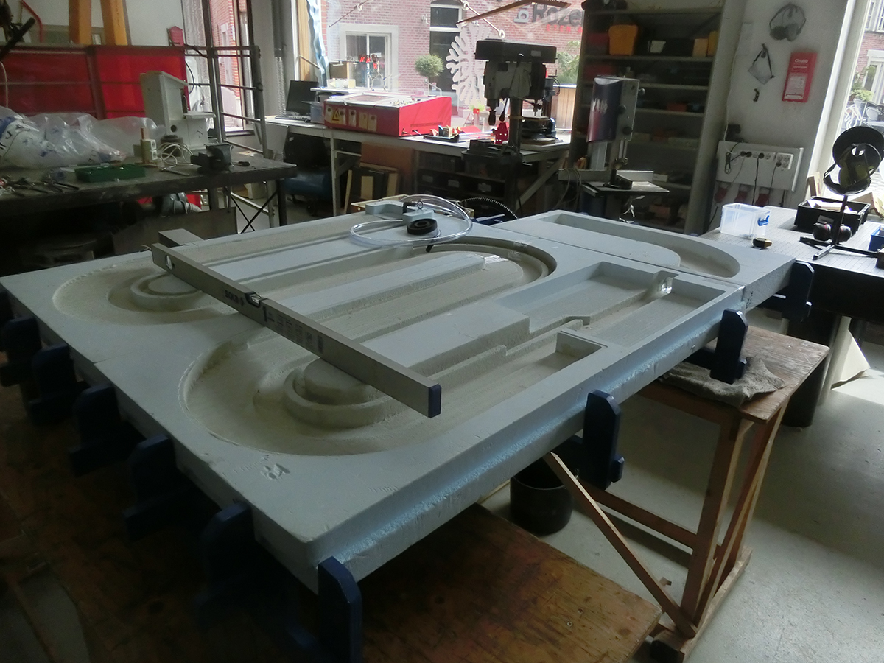
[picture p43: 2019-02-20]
figs/20160108CIMG1782copy.jpg

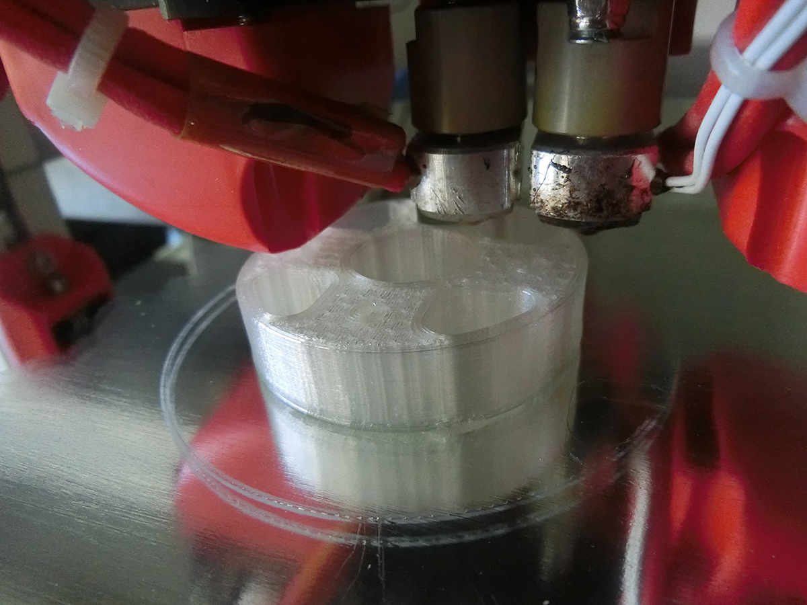
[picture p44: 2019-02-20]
figs/20162608CIMG2251copy.jpg

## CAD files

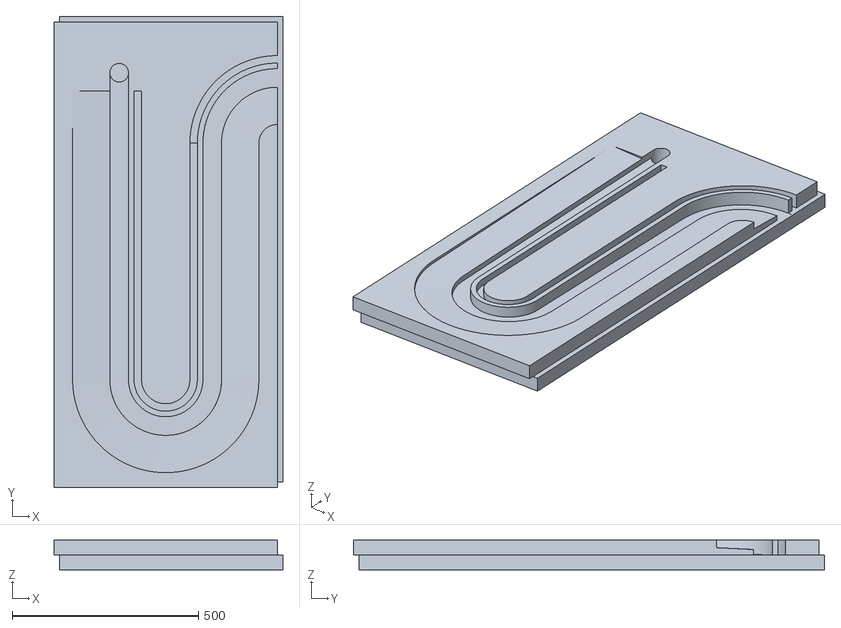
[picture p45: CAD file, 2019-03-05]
topodrawings/wetropolisV1aug2016feb2017foamupstream.stl
615.0 x 1265.0 x 80.0

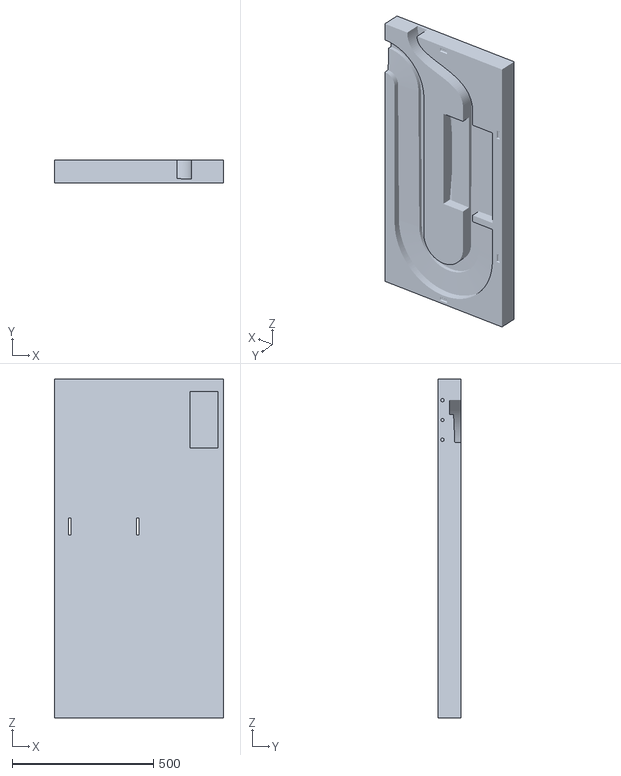
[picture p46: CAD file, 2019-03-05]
topodrawings/WetropolisBOTTOMHalf2017NFM.STL
600.0 x 80.0 x 1200.0

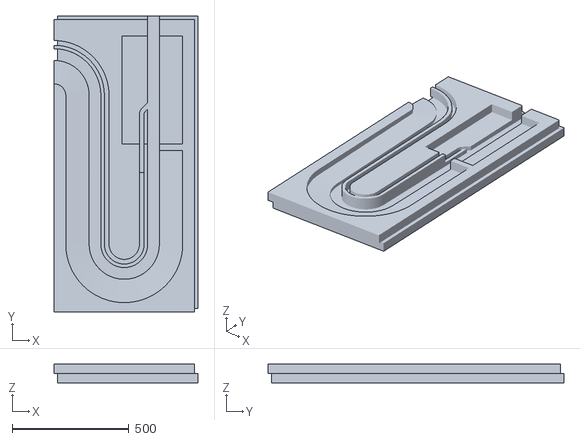
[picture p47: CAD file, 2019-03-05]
topodrawings/wetropolisV1aug2016feb2017foamdownstream.stl
615.0 x 1265.0 x 80.0

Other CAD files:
topodrawings/FoamBlockTOPHalf2017NFM.STL
topodrawings/FoamBlockTOPHalf2017NFM (1).STL

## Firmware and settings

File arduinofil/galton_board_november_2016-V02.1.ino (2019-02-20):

/* 
  ----
  copyright: 
  crative commons, free to use (non commercial, eduactional)
  author: 
  wout zweers
  zweers@dds.nl
  
  version V02, nov 2016
  ----
  doel programma: 
  
  aansturen galton board kogels, leds, relais en servo's.
  ir sensors in galton board sturen pomprelais aan.
  passerende kogel laat led bij baan oplichten
  en triggert relais welke pomp aan / uitschakelt
  gb1: groene leds, regen, lanes 5-8
  gb2: amber leds, locatie, lanes 1-4
  
  goed getest met bord 1 en 2 op 11 nov 2016
  
  circuit, print lay out, constructie galton board: github, grabcad
 
  componenten: 
  
  board: arduino mega
  ir sensors: adafruit breakbeam #2167 
  servo: Hitec HS-311 
  leds: 15mA, 6V, 330ohm resistor 
  relay: relay module 2 relais low level trigger
  external power supply: 6V 1.5A (5V is not enough)

*/
  
#define ledPin 13

#define led8Pin 44 // leds gb1 = rain
#define led7Pin 46 
#define led6Pin 48
#define led5Pin 50
#define led4Pin 42 // leds gb2 = location
#define led3Pin 40
#define led2Pin 38
#define led1Pin 36

#define Servo1Pin 53 // gb1 servo
#define Servo2Pin 37 // gb2 servo
   
//
// Now (check): no rain, lake, moor, both; must become lake, both, moor, no rain so switch numbers accordingly for baan/lane. Change stickers/names accordingly.
// No need to change ledxPin
// Not clear yet whether this is the right change to probability
//
#define baan1Pin 39 // ir detectors gb2 = location
#define baan2Pin 41
#define baan3Pin 43
#define baan4Pin 45
#define baan5Pin 51 // ir detectors gb1 = rain
#define baan6Pin 49
#define baan7Pin 47
#define baan8Pin 52 // niet op volgorde ivm aansluiting foutje (NC omgewisseld ) 

#define moorRelayPin 22 // relais 1 moor
#define lakeRelayPin 23 // relais 2 lake

// variables will change:

int rain1Time=1;// rain time in seconds for slot 1, 2, 3, 4
int rain2Time=2;
int rain3Time=4;
int rain4Time=9; // was 8
int pumpCycleTime=10; // was 8 totale tijd vd pompcyclus in seconds

int baan1State = 0;
int baan2State = 0;
int baan3State = 0;
int baan4State = 0;
int baan5State = 0;
int baan6State = 0;
int baan7State = 0;
int baan8State = 0;

int inrolHoek=104;    //servo:  109 (inrol positie) en  79 (uitrolpositie) zijn goede waarden voor beide borden
int uitrolHoek = 77;
int detectieBordEen=0;
int detectieBordTwee=0;

int tellerEen=0; //voor de statistiek
int tellerTwee=0;
int tellerDrie=0;
int tellerVier=0;
int tellerVijf=0;
int tellerZes=0;
int tellerZeven=0;
int tellerAcht=0;

int totaalRun=1; // begin bij 1
int percentage;

int rain=0; // bepaalt pomp duur 1, 2, 4, 8 tijdeenheden
int moor=1; // bepaalt pomp locatie: m0or of lake
int lake=1;
int pompDuur=0;
int wachtTijd=0;
 
void setup() 
{
  //pomp uit
  digitalWrite(moorRelayPin, HIGH); // zet pompen  uit
  digitalWrite(lakeRelayPin, HIGH);
    
  pinMode(led1Pin, OUTPUT); // nog aanzetten
  pinMode(led2Pin, OUTPUT);
  pinMode(led3Pin, OUTPUT);
  pinMode(led4Pin, OUTPUT);  
  pinMode(led5Pin, OUTPUT); 
  pinMode(led6Pin, OUTPUT);
  pinMode(led7Pin, OUTPUT);
  pinMode(led8Pin, OUTPUT); 
  pinMode(ledPin, OUTPUT); 
  pinMode(moorRelayPin, OUTPUT);
  pinMode(lakeRelayPin, OUTPUT);
      
  digitalWrite(baan1Pin, HIGH); // nog aanzetten. turn on the pullup
  digitalWrite(baan2Pin, HIGH); 
  digitalWrite(baan3Pin, HIGH); 
  digitalWrite(baan4Pin, HIGH);
  digitalWrite(baan5Pin, HIGH); // turn on the pullup
  digitalWrite(baan6Pin, HIGH); 
  digitalWrite(baan7Pin, HIGH); 
  digitalWrite(baan8Pin, HIGH);
   
  Serial.begin(9600);

   draaiServo(inrolHoek); // laden kogel in wiel
   
  // testen van  leds, pompen, servo 
  pomptest (); // led 13 knippert, daarna pompen allebei even aan (3 sec)
  ledsAan(); // led test. alle leds moeten branden
  draaiServo(uitrolHoek); //test bij opstarten, eerste kogel valt
  delay(5000); //voldoende lang om kogel langs sensor te laten rollen zonder detectie te triggeren  
  draaiServo(inrolHoek); // als je deze uitzet wacht programma tot je zelf de eerste kogel er in gooit
  
  ledsUit(); 
 
}
 
// Main Program arduino looks for first for setup (all definitions, priming to get ready) and then loop
void loop(){
   
draaiServo(uitrolHoek); // kogel valt uit wiel (ongeveer 0.5 sec voor dit commando nodig. kogel is dan nog ruim boven detectors

//while (detectieBordEen==0)// nog aanvullen met detectiepoort twee or boolean - scannen poorten. dit is een snelle loop en kort genoeg om detectie te garanderen
while (detectieBordEen==0 || detectieBordTwee==0) // er wordt gescand tot beide detecties plaats hebben gevonden en indicators hoog zijn. als twee borden aan zijn gesloten nodig
    {
      baan1State = digitalRead(baan1Pin); // gb2, low = straal onderbroken = detectie
      baan2State = digitalRead(baan2Pin);
      baan3State = digitalRead(baan3Pin);
      baan4State = digitalRead(baan4Pin);
      baan5State = digitalRead(baan5Pin); // gb 1, low = straal onderbroken = detectie
      baan6State = digitalRead(baan6Pin);
      baan7State = digitalRead(baan7Pin);
      baan8State = digitalRead(baan8Pin);
      
      
      // boolean && om te voorkomen dat evt twee kogeltjes twee keer triggeren. alleen eerste kogel verandert waarden 
      // Here you can make a change 
      if (baan1State == LOW && detectieBordTwee==0) {detectieBordTwee=1; digitalWrite(led1Pin, HIGH); Serial.println("baan1 "); tellerEen+=1;  moor = 0; lake = 1;} // locatiefunctie
      if (baan2State == LOW && detectieBordTwee==0) {detectieBordTwee=1; digitalWrite(led2Pin, HIGH); Serial.println("baan2 "); tellerTwee+=1; moor = 1; lake = 1;}
      if (baan3State == LOW && detectieBordTwee==0) {detectieBordTwee=1; digitalWrite(led3Pin, HIGH); Serial.println("baan3 "); tellerDrie+=1; moor = 1; lake = 0;}
      if (baan4State == LOW && detectieBordTwee==0) {detectieBordTwee=1; digitalWrite(led4Pin, HIGH); Serial.println("baan4 "); tellerVier+=1; moor = 0, lake = 0;}
     
      if (baan5State == LOW && detectieBordEen==0) {detectieBordEen=1; digitalWrite(led5Pin, HIGH); Serial.println("baan5 "); tellerVijf+=1;  rain=rain1Time;}// regenfunctie.
      if (baan6State == LOW && detectieBordEen==0) {detectieBordEen=1; digitalWrite(led6Pin, HIGH); Serial.println("baan6 "); tellerZes+=1;   rain=rain2Time;}
      if (baan7State == LOW && detectieBordEen==0) {detectieBordEen=1; digitalWrite(led7Pin, HIGH); Serial.println("baan7 "); tellerZeven+=1; rain=rain3Time;}
      if (baan8State == LOW && detectieBordEen==0) {detectieBordEen=1; digitalWrite(led8Pin, HIGH); Serial.println("baan8 "); tellerAcht+=1;  rain=rain4Time;}
    }
    
 draaiServo(inrolHoek); // kogel klaarleggen

 statistiek(); // statistiek naar seriele monitor schrijven. voor calibratie en controle
   
 pompFunctie(rain,pumpCycleTime,lake,moor);
  //delay(1700); // wachttijd als pompfunctie niet aan staat
 ledsUit(); // doe alle leds uit
 detectieBordEen=0; // herstart de valcyclus
 detectieBordTwee=0;
          
  }

  // hieronder de functions pomptest, pompFunctie, statistiek, ledsAan, ledsUit, draaiServo
  
 void  pomptest (){
  // -----
  // zorgt voor korte test bij opstarten: pompen gaan na elkaar 3 sec aan. led 13 knippert 3x voor het pompen begint
  // -----
  digitalWrite(lakeRelayPin, HIGH);
  digitalWrite(moorRelayPin, HIGH);
  digitalWrite(ledPin, HIGH);// led knippert drie keer
  delay(250);
  digitalWrite(ledPin, LOW);
  delay(250);
  digitalWrite(ledPin, HIGH);
  delay(250);
  digitalWrite(ledPin, LOW);
  delay(250);
  digitalWrite(ledPin, HIGH);
  delay(250);
  digitalWrite(ledPin, LOW);
  delay(250);
  digitalWrite(moorRelayPin, LOW); //zet moor pomp aan (low = aan)
  delay (3000);
  digitalWrite(moorRelayPin, HIGH);
  digitalWrite(lakeRelayPin, LOW); //zet lakepomp aan (low = aan)
  delay(3000);
  digitalWrite(lakeRelayPin, HIGH);
  
 } 
  

void pompFunctie(int rain, int pumpCcycleTime, int moor, int lake){
    // -----
    // bepaalt welke pomp aan gaat en hoe lang
    // -----
  if (moor == 1) digitalWrite(moorRelayPin, LOW); // zet pomp aan (low = aan) switch on when low
  if (lake == 1) digitalWrite(lakeRelayPin, LOW); 
  pompDuur = rain* 1000; //msec
  delay(pompDuur); 
  
  digitalWrite(moorRelayPin, HIGH); // zet pompen weer uit en wacht
  digitalWrite(lakeRelayPin, HIGH);
   
  wachtTijd = pumpCycleTime*1000-pompDuur; // resttijd in cyclus , msec
  if (wachtTijd>0) delay(wachtTijd); // alleen positieve wachttijden voor delay
 
  
 }

void statistiek(){ 
    // -----
    // stuurt gegevens over passage door: welke baan en percentage van totaal en houdt aantal runs bij. 
    // geeft daaruit volgende status voor pomp (moor, lake, rain door)
    // -----
   Serial.print("runnr:  ");
   Serial.println(totaalRun);
    // statistieken
 
   Serial.print("baan1 "); //gb2
   Serial.print(tellerEen);
   Serial.print(" percentage ");
   percentage = 100*tellerEen/totaalRun;
   Serial.println(percentage);
   
   Serial.print("baan2 ");
   Serial.print(tellerTwee);
   Serial.print(" percentage ");
   percentage = 100*tellerTwee/totaalRun;
   Serial.println(percentage);
   
   Serial.print("baan3 ");
   Serial.print(tellerDrie);
   Serial.print(" percentage ");
   percentage = 100*tellerDrie/totaalRun;
   Serial.println(percentage);
   
   Serial.print("baan4 ");
   Serial.print(tellerVier);
   Serial.print(" percentage ");
   percentage = 100*tellerVier/totaalRun;
   Serial.println(percentage);
 
   Serial.print("baan5 "); //gb1
   Serial.print(tellerVijf);
   Serial.print(" percentage ");
   percentage = 100*tellerVijf/totaalRun;
   Serial.println(percentage);
   
   Serial.print("baan6 ");
   Serial.print(tellerZes);
   Serial.print(" percentage ");
   percentage = 100*tellerZes/totaalRun;
   Serial.println(percentage);
   
   Serial.print("baan7 ");
   Serial.print(tellerZeven);
   Serial.print(" percentage ");
   percentage = 100*tellerZeven/totaalRun;
   Serial.println(percentage);
   
   Serial.print("baan8 ");
   Serial.print(tellerAcht);
   Serial.print(" percentage ");
   percentage = 100*tellerAcht/totaalRun;
   Serial.println(percentage);
   
   Serial.println("----- ");
     
   totaalRun+=1; // totaal aantal runs
   
   Serial.print("rain= "); // voor debuggen
   Serial.println(rain);
   Serial.print("lake= "); 
   Serial.println(lake);
   Serial.print("moor= "); 
   Serial.println(moor);
}

void ledsAan(){
   // -----
   // zet alle leds aan op de galton boards
   // -----
  digitalWrite(led5Pin, HIGH); //alle leds aan voor test
  digitalWrite(led6Pin, HIGH);
  digitalWrite(led7Pin, HIGH);
  digitalWrite(led8Pin, HIGH);
 
  digitalWrite(led1Pin, HIGH);
  digitalWrite(led2Pin, HIGH);
  digitalWrite(led3Pin, HIGH);
  digitalWrite(led4Pin, HIGH);
  
}

void ledsUit(){
    // -----
    // zet alle leds uit op de galton boards
    // -----
  digitalWrite(led5Pin, LOW); // doof alle leds
  digitalWrite(led6Pin, LOW);
  digitalWrite(led7Pin, LOW);
  digitalWrite(led8Pin, LOW);
  digitalWrite(led1Pin, LOW);
  digitalWrite(led2Pin, LOW);
  digitalWrite(led3Pin, LOW);
  digitalWrite(led4Pin, LOW);
  }
  
void draaiServo(int draaiHoek) 
{
  // ---
  // laat servo's naar begin en eindhoek draaien om het kogeltje in de baan te brengen. servo's 1 en 2 worden identiek aangestuurd
  // functie laat de servo een aantal keer draaien in de richting van de gewenste hoek. dit is nodig omdat per keer slechts een kleine verdraaing wordt uitgevoerd. 
  // als je dit 25 x doet dan is de volledige draai (180 graden ) gemaakt. 30 graden ongeveer in 15x
  //-----
    int count=0; // teller voor het aantal herhalingen
    int pulsLengte; //waarden pulslengte: tussen 500 en 2500. 1500 is middenstand / neutraal
    
    pulsLengte=map(draaiHoek,0,180,500,2500); // zet hoek in graden om naar pulslengtre voor de servo. hoek afhankelijk van servo. meestal tussen 0 en 180
    
    while (count<16)
    {
      count+=1; 
      
      // commando blijven schrijven naar servopin voor verdraaien, dit moet herhaald worden anders stopt servo voordat eindstand bereikt is (geen geheugen in servo) 
      // ongeveer 15 keer moet genoeg zijn. kan korter bij kleine hoekverschillen. tijdsduur ongeveer 0.5 sec bij count 15
      // Update Onno 06-01-2018: first did servo1 and then servo2 to ease power usage
      
      pinMode(Servo1Pin, OUTPUT);      // bepaal dat ServoPin output pin is
      digitalWrite(Servo1Pin, HIGH);   // start puls
      delayMicroseconds(pulsLengte);   // pulslengte bepaalt eindpositie (goal)
      digitalWrite(Servo1Pin, LOW);    // beeindig puls
      pinMode(Servo2Pin, OUTPUT); 
      digitalWrite(Servo2Pin, HIGH);
      delayMicroseconds(pulsLengte);   // pulslengte bepaalt eindpositie (goal)
      digitalWrite(Servo2Pin, LOW);
      delay(25); // deze tijd niet veranderen ivm goed functioneren van de servo
    }
    count=0; // reset counter
}

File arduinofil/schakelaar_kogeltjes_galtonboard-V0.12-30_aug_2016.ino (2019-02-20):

/*
  version 12

  Implemented random number generator to emulate Galton board runs
  added timer (2 sec) which turns on random gen if no detection happened after certainn period (fall time of ball, about two seconds)

  Introduction:

  purpose of this program

  - bediening van arduino mega om wetropolis waterhoogtes te meten, Galton board te gebruiken om pompen moor en lake aan en uit te zetten.
   doorsturen via seriele poort van meetwaarden.
  - operation arduino to measure water level, use of galton board to operate pumps for moor and lake (on or off)

  author: wout zweers aug 2016
  contact: zweers@dds.nl

  licence: open source program,
  warranty: this program may be used as is, no warranties are given.

  // Program organisation:
  //
  // --- 1 listing of pins, variables ---
  // --- 2 measure sensor values ---
  // --- 3 determine pump times and location, start and stop pumps, send values and waterlevels to serial port---
  // --- 4 send waterlevel values to serial port as feedback or for logging --- moved to 3 in V0.5
  // --- 5 reset values galton board
  // --- 6 transport ball implemented in version 0.4

  Description of parts and their function:
  - Galton board: a steel ball falls through the Galton board and passes 2 sensors with 2x4=8 possibilities.
  the passage determines duration (4 choices, e.g.: 1,2,4,9s) and location of rain (4 choices: ),
  simulated by two pumps (equivalent to location of rainfall: moor or lake/reservoir)
  that are switched on or off for a certain time (equivalent to intensity of rain fall).
  - Waterlevel sensors: 6 steel pins with tips on various levels hang in or above the water. falling or raising water level let a (tiny)
  current flow through the pins which is sensed.
  The value (on or off) determines where there is water. The highest positive read out indicates the water surface. Water leves are measued at two places.
  - An ultrasonic sensor is used as an optional measurement.  It can be used aditionally to the water level sensor pins or as a sensor for the water level in the lake
  The values are sent to the serial port and can be logged with either the serial monitor or with a logging program to store the data in a file

  The circuits:
  --- galton board:---
  light sensors consisting of LDR (value app 1 KOhm ( resistive value when lit) to >20 KOhm ( when dark)
  Resistor 2.2K connected between digital pins and +5V on arduino
  wire from pins to LED
  wire from pin gnd on arduino other side LDR

  --- Servomotor ---
  For transport of steel ball into galton board will free one ball every cycle (cycle time should be around 10 seconds). Drop first ball by hand to start.

  --- Water level measurement ---
  Between two pins is typically a resistance measurable of app. 1MOhm. Not connected pins do not conduct electricity.
  Resistor 1M connected between digital pins and +5V on arduino
  wire from pins to waterrlevelpin
  wire from pin gnd on arduino other side waterlevelpin

  --- Indication to close lock manually ---
   optianally indication for manually closing a lock: 330ohm for led for locks no 1, 2, 3, 4 (pin 32, 33 , 34, 35)
   indication LED, connected from digital pin 13 to ground
   digital pins 22-53 are on one header on the arduino mega

  --- lijst of pin connections: ---

  servoPin = 9
  ledPin = 13

  Galton board:
  baanStartPin = 22 // sensor is replaced to lane 3 = baan3 = RM
  baan1Pin = 23 LU = linksonder bovenste banen
  baan2Pin = 24 LM
  baan3Pin = 25 RM // changed this to p22 because of rotten detector on p25. baanStartPin will not function, but that is not a problem for the detection
  baan4Pin = 26 RT = rechtsboven

  baanMiddenPin = 27 NC

  baan5Pin = 28 LT = linksboven onderste banen
  baan6Pin = 29 LM
  baan7Pin = 30 RM
  baan8Pin = 31 RU = rechtsonder

  Locks:
  lock1Pin = 32 (in kanaal) eventually 330ohm for led
  lock2Pin = 33
  lock3Pin = 34
  lock4Pin = 35 (in rivier)

  Valve lake:
  spillwayPin = 36

  Waterlevels:
  levelSensorA1 = 37
  levelSensorA2 = 38
  levelSensorA3 = 39
  levelSensorA4 = 40
  levelSensorA5 = 41
  levelSensorA6 = 42

  levelSensorB1 = 43
  levelSensorB2 = 44
  levelSensorB3 = 45
  levelSensorB4 = 46
  levelSensorB5 = 47
  levelSensorB6 = 48

  Transport balls:
  ballTriggerPin = 49 // nc, servo is used on pin 9

  Relais pumps:
  moorRainPin = 50
  lakeRainPin = 51

  optionele waterlevel (ultrasonic sensor)

  levelSensor trigger = 52 blue
  levelSensor echo = 53 yellow

  Created 19 Aug 2016 by Wout Zweers
  Revised v3 27-30 Aug 2016

*/

// Servomotor voor kogeltransport/for transport steel balls. code komt uit voorbeeld sweep/code example sweep

#include <Servo.h> // calling servo library

Servo myservo;  // create servo object to control a servo
// twelve servo objects can be created on most boards

int pos = 0;    // variable to store the servo position

//einde servomotor

// --- definition of pins ---

const int servoPin = 9; //servo kogeltransport wordt met pin 9 aangestuurd (nodig voor oude arduino versies)
const int ledPin = 13; // pin 13 is gewoonlijk voor de led (op pcb board aanwezig)

// Galton board sensors, 10 sensors, (baanMidden en baanTop onnodig en daarom Not Connected, dus 8 in gebruik)
// detectors BaanxxPin indicate through which lane balls have fallen

const int baanStartPin = 25; // toegangsbaan galton board exchanged this with nr 25.
const int baan1Pin = 23; // rain amount
const int baan2Pin = 24;
const int baan3Pin = 22; // exchanged with sensor from baanStart
const int baan4Pin = 26;
const int baanMiddenPin = 27; // lichtsluis tussen onderste en bovenste deel Galton board. (NC = not connected)
const int baan5Pin = 28; // location of rain
const int baan6Pin = 29;
const int baan7Pin = 30;
const int baan8Pin = 31;

const int lock1Pin = 32; // lock 1 stuw led aan. optioneel later toevoegen electrische klep
const int lock2Pin = 33;
const int lock3Pin = 34;
const int lock4Pin = 35;

const int spillwayPin = 36; // reservoir uitlaat klep gesloten of led aan, optioneel later toevoegen electrische klep

// Waterdiepte/water level sensors, 2 x 6 meetpennen op/on locatie/location A en B

const int levelSensorA1 = 37; // locatie A
const int levelSensorA2 = 38;
const int levelSensorA3 = 39;
const int levelSensorA4 = 40;
const int levelSensorA5 = 41;
const int levelSensorA6 = 42;
const int levelSensorB1 = 43; // locatie B
const int levelSensorB2 = 44;
const int levelSensorB3 = 45;
const int levelSensorB4 = 46;
const int levelSensorB5 = 47;
const int levelSensorB6 = 48;

// 1 trigger voor knikker transport of vrijgave, elke 10 sec een trigger. kan een led aan/uitzetten of een mechaniek

const int ballTriggerPin = 49; // wordt niet gebruikt als servo werkt

const int moorRainPin = 50; // schakelt pomp aan of uit via relais
const int lakeRainPin = 51; // 2 optionele ultrasone sensors voor waterdiepte. nauwkeurigheid 3 mm
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
